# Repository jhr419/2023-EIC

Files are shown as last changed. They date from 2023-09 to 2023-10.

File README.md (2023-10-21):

# BUPT EIC  

北京邮电大学鸿雁战队2023工程创新与实践大赛电控代码仓库

## 使用说明

上电后，调整机械臂到指定位置后，按下A版上的白键锁定

### 通信接口说明

---

usart6 - 与NUC的收发和交流\
uart8 - 与action的收发和交流\
uart7 - 调试使用接口\
can - 和电机交互\
can1 - MS4015\
can2 - M2006&M3508

---

## Work To be done & optimized

· **待完成** 影响是否能够完成项目的事项\
1.完成2006ECD锁定\
2.添加转盘函数\
这俩做完就差不多做完了\
· **待优化** 对已有的功能进行性能提高/模块解耦/可维护性增强\
1.任务延时调整\
2.任务流程优化\
2.2006 pid调整\
· **待添加** 无关紧要，锦上添花

## 开发准则

### 禁止过度摸鱼

### 禁止在临界区使用os延迟

#### 临界资源

指一次仅仅允许一个线程访问的共享资源，它可以是一个具体的硬件设备，也可以是一个变量，可以是缓冲区等，这些都称为临界资源，或者共享资源，多个任务同时运行，只能允许一个任务访问的资源。

#### 临界区

每个进程中访问临界资源的那段代码称为临界区，
每次只允许一个进程进入临界区，进入后，不允许其他进程进入。不论是硬件临界资源还是软件临界资源，多个进程必须互斥的对它进行访问。多个进程涉及到同一个临界资源的的临界区称为相关临界区。使用临界区时，一般不允许其运行时间过长，只要运行在临界区的线程还没有离开，其他所有进入此临界区的线程都会被挂起而进入等待状态。

### 禁止在使用开发版自带的xt30接口接电机

电机的反向电动势可能会烧毁开发板。

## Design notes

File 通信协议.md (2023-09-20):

# 通信协议 v1.0

## 串口配置

通信方式是串口，配置为波特率 115200，8 位数据位，1 位停止位，无硬件流控，无校验位。

## 通信协议格式

|帧头|数据|帧尾|
|:-:|:-:|:-:|
|frame_header(5-Byte)|data(n-Byte)|frame_tail(2-Byte,CRC-16,仅校验data)|

## frame_header格式

|SOF|cmd_id|length|CRC-8|
|:-:|:-:|:-:|:-:|
|0xA5(1-Byte)|命令码(1-Byte)|data长度(2-Byte)|帧头校验(1-Byte)|

## 命令码说明

|cmd_id|数据类型|
|:-:|:-:|
|0x01|trolley_info_t|
|0x02|move_cmd_t|
|0x03|pinch_cmd_t|

## 数据类型详情

    typedef struct
    {
        float32 x_abs;
        float32 y_abs;
        float32 angle_abs; // 角度制
        int16_t block_num; // 车载物块数量，上限为3
    } trolley_info_t;

上述坐标以下图坐标系为参考，角度信息以x轴正方向为0度，取值范围（-180,180]。
（下图仅作示意，具体位置待实际测量）
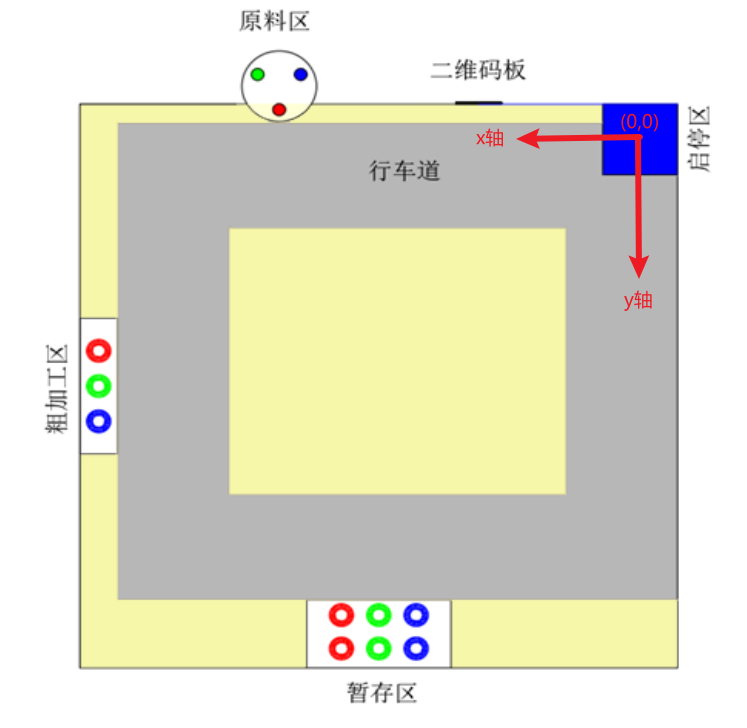
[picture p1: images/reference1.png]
reference1


    typedef struct
    {
        float32 vx_err;
        float32 vy_err;
        float32 vw_err;
    } move_cmd_t;

上述信息均为相对值，相对于车的当前位置及朝向。或者说，是可以直接用于PID算法的error值。

    typedef struct
    {
        uint8_t act_id; // act_id对应动作编号（1-抓取，2-放置）
    } pinch_cmd_t;

 ## 动作编号说明

|cmd_id|数据类型|
|:-:|:-:|
|0x01|ARM1_GRAP1|
|0x02|ARM2_GRAP1|
|0x03|ARM2_PLACE1|
|0x04|ARM2_PLACE2|

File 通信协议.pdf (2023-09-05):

通信协议.md | 9/4/2023

# 通信协议

## 串⼝配置

通信⽅式是串⼝，配置为波特率 115200，8 位数据位，1 位停⽌位，⽆硬件流控，⽆校验位。

## 通信协议格式

帧头 | 数据 | 帧尾
frame_header(5-Byte) data(n-Byte) frame_tail(2-Byte,CRC-16,仅校验data)

## frame_header格式

SOF | cmd_id | length | CRC-8

0xA5(1-Byte) 命令码(1-Byte) data⻓度(2-Byte) 帧头校验(1-Byte)

## 命令码说明

cmd_id | 数据类型
0x01 | trolley_info_t
0x02 | move_cmd_t
0x03 | pinch_cmd_t

## 数据类型详情

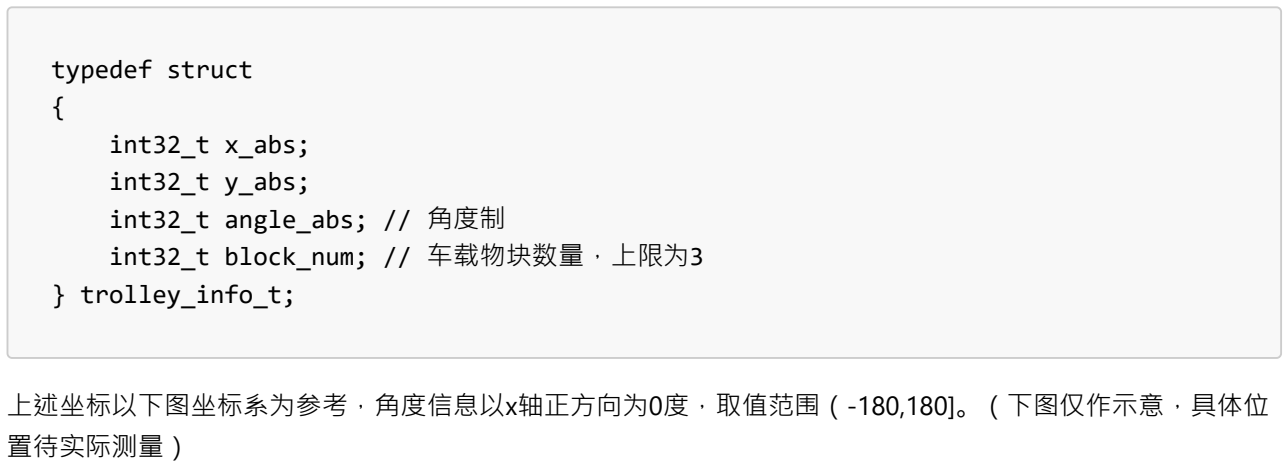
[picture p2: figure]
typedef struct {; int32_t x_abs; int32_t y_abs; int32_t angle_abs; // ⾓度制 int32_t block_num; // ⻋载物块数量，上限为3 } trolley_info_t;; 上述坐标以下图坐标系为参考，⾓度信息以x轴正⽅向为0度，取值范围（-180,180]。 （下图仅作⽰意，具体位 置待实际测量）

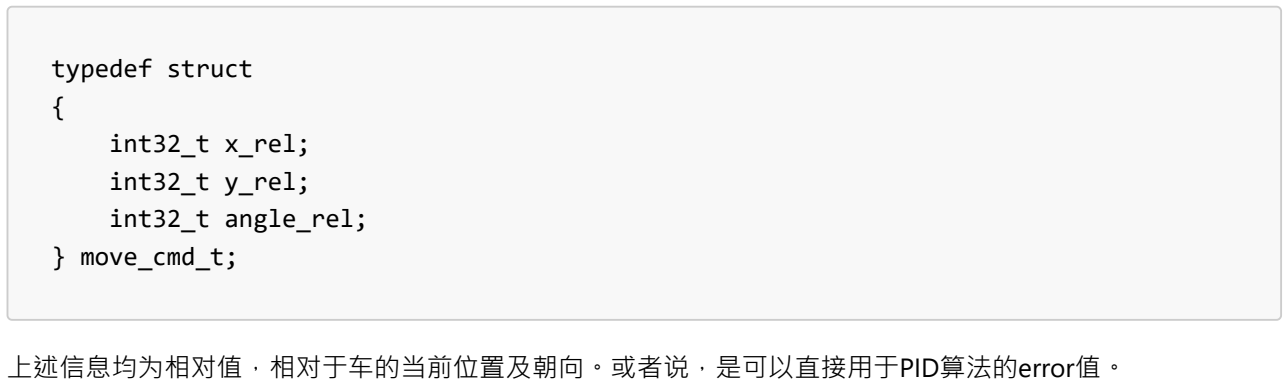
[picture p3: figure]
typedef struct {; int32_t x_rel; int32_t y_rel; int32_t angle_rel; } move_cmd_t;; 上述信息均为相对值，相对于⻋的当前位置及朝向。或者说，是可以直接⽤于PID算法的error值。
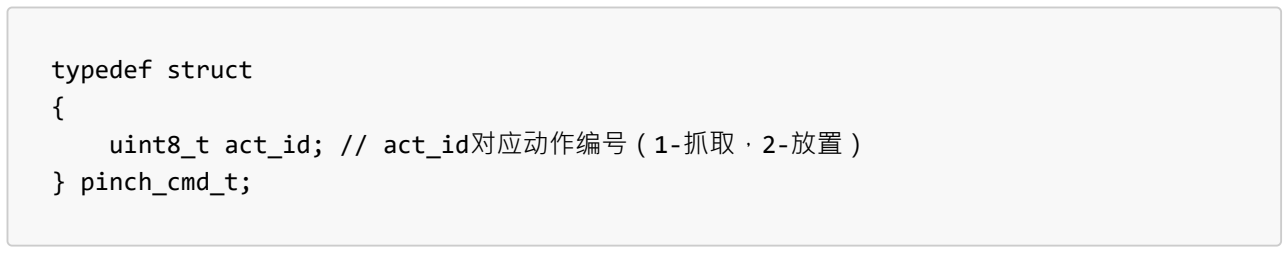
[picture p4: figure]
typedef struct {; uint8_t act_id; // act_id对应动作编号（1-抓取，2-放置） } pinch_cmd_t;

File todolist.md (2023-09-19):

任务流程汇总
全场定位坐标转换为整车坐标 这部分代码得今天完成
1. pid算法选择
2. 速度规划算法（简单方案，复杂方案）现敲定以双环pid，或者位置环+读取编码器的值获取
3. 底盘任务（跑定点 ，旋转固定角度同时走位置 , 换算坐标）
4. 舵机的控制及设计抓取和放置流程（打开不同电机计时器，设置pid控制）
5. 机械臂任务目前有四种，抓取台上物品，抓取车上物块，放置在地上，放置在物块上

这次需要突破的问题，就是将以前的模糊值转化为真实值
然后制定完整的机器人框架，将代码写成库的形式，可能需要审视一下代码，将其中复用性差的部分移除

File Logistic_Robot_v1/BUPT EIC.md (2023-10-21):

# BUPT EIC  

北京邮电大学鸿雁战队2023工程创新与实践大赛电控代码仓库

## 使用说明

上电后，调整机械臂到指定位置后，按下A版上的白键锁定

## 机械臂动作说明

### 旋转2006简称Ⅰ，升降2006简称Ⅱ

#### 运行前需Ⅰ要标定的位置

| 编号 | a | b |
| :-----:| :----: |  :----: |
| 描述 | 向内 |向外|

起始位置应该与机械臂最近的一条边垂直，且正对着4015载物盘

#### 运行前升降要标定的位置

| 编号 | 1 | 2 | 3 | 4 | 5 | 6 | 7 | 8 |
| :-----:| :----: | :----: | :----: | :----: | :----: | :----: | ---| ---|
| 描述 | 车内物料抓取预备点 |车内物料抓取点| 原料区物料抓取预备点 |原料区物料抓取点 | 地面物料预备点 | 地面取放点 | 细加工区叠放预备点 | 细加工区放置点 |

---

### 机械臂任务码设计及流程

基本动作：

1. arm底盘旋转：初始化，向外，向内

2. 升降机构：初始化（车上物料盘），向上，向下

3. 物料盘：初始化，物料加一

4. 摄像头舵机：二维码位置，物料位置

5. 机械爪：打开，关闭

### 启动区

task0: 初始化任务：

	物料底盘初始化，arm底盘初始化，升降初始化（略高于物料），舵机二维码位置

### 二维码区

task1：读取二维码任务：

	arm底盘向外， 机械爪打开

### 原料区

{

	task2：预抓取：

		 舵机物料位置，升降预备抓取位置，（车预备位置）

	task3：原料区抓取：

		升降降低位置，机械爪关闭

	task4：物料放置车上：

		升降抬升位置，arm底盘向内，升降降低至放置位置，机械爪打开，升降抬升

	task5：

		物料加一

}

task2-5执行三次

### 粗加工区

{

	task6：预放置：

		arm底盘向内，升降初始化（略高于物料），机械爪打开，物料盘转至对应物料，升降向下至物料处，机械爪关闭，升降抬升位置，arm底盘向外

	task7：放置：

		升降降低，机械爪打开，升降抬升

}

task6-7执行三次

{

	task8：预抓取：

		 arm底盘向外，升降预备抓取位置，（车预备位置）

	task9：抓取：

		升降降低位置，机械爪关闭

	task10：物料放置车上：

		升降抬升位置，arm底盘向内，升降降低至放置位置，机械爪打开

	task11：

		物料加一

}

task8-11执行三次

### 细加工区

{

	task12：预放置：

		arm底盘向内，升降初始化（略高于物料），机械爪打开，物料盘转至对应物料，升降向下至物料处，机械爪关闭，升降抬升位置，arm底盘向外

	task13：放置：

		升降降低，机械爪打开，升降抬升

}

task12-13执行三次

## 进入下一轮原料区

原料区、粗加工区任务重做

### 叠放

{

	task14：预放置：

		arm底盘向内，升降初始化（略高于物料），机械爪打开，物料盘转至对应物料，升降向下至物料处，机械爪关闭，升降抬升位置，arm底盘向外

	task15：放置：

		升降降低，机械爪打开，升降抬升

}

task14-15执行三次

### 通信接口说明

---

usart6 - 与NUC的收发和交流\
uart8 - 与action的收发和交流\
uart7 - 调试使用接口\
dbus - 遥控器接口\
can - 和电机交互\
can1 - MS4015\
can2 - M2006&M3508

---

## Work To be done & optimized

· **待完成** 影响是否能够完成项目的事项\
· **待优化** 对已有的功能进行性能提高/模块解耦/可维护性增强\
· **待添加** 无关紧要，锦上添花

## 开发准则

### 禁止过度摸鱼

### 禁止在临界区使用os延迟

#### 临界资源

指一次仅仅允许一个线程访问的共享资源，它可以是一个具体的硬件设备，也可以是一个变量，可以是缓冲区等，这些都称为临界资源，或者共享资源，多个任务同时运行，只能允许一个任务访问的资源。

#### 临界区

每个进程中访问临界资源的那段代码称为临界区，
每次只允许一个进程进入临界区，进入后，不允许其他进程进入。不论是硬件临界资源还是软件临界资源，多个进程必须互斥的对它进行访问。多个进程涉及到同一个临界资源的的临界区称为相关临界区。使用临界区时，一般不允许其运行时间过长，只要运行在临界区的线程还没有离开，其他所有进入此临界区的线程都会被挂起而进入等待状态。

### 禁止在使用开发版自带的xt30接口接电机

电机的反向电动势可能会烧毁开发板。

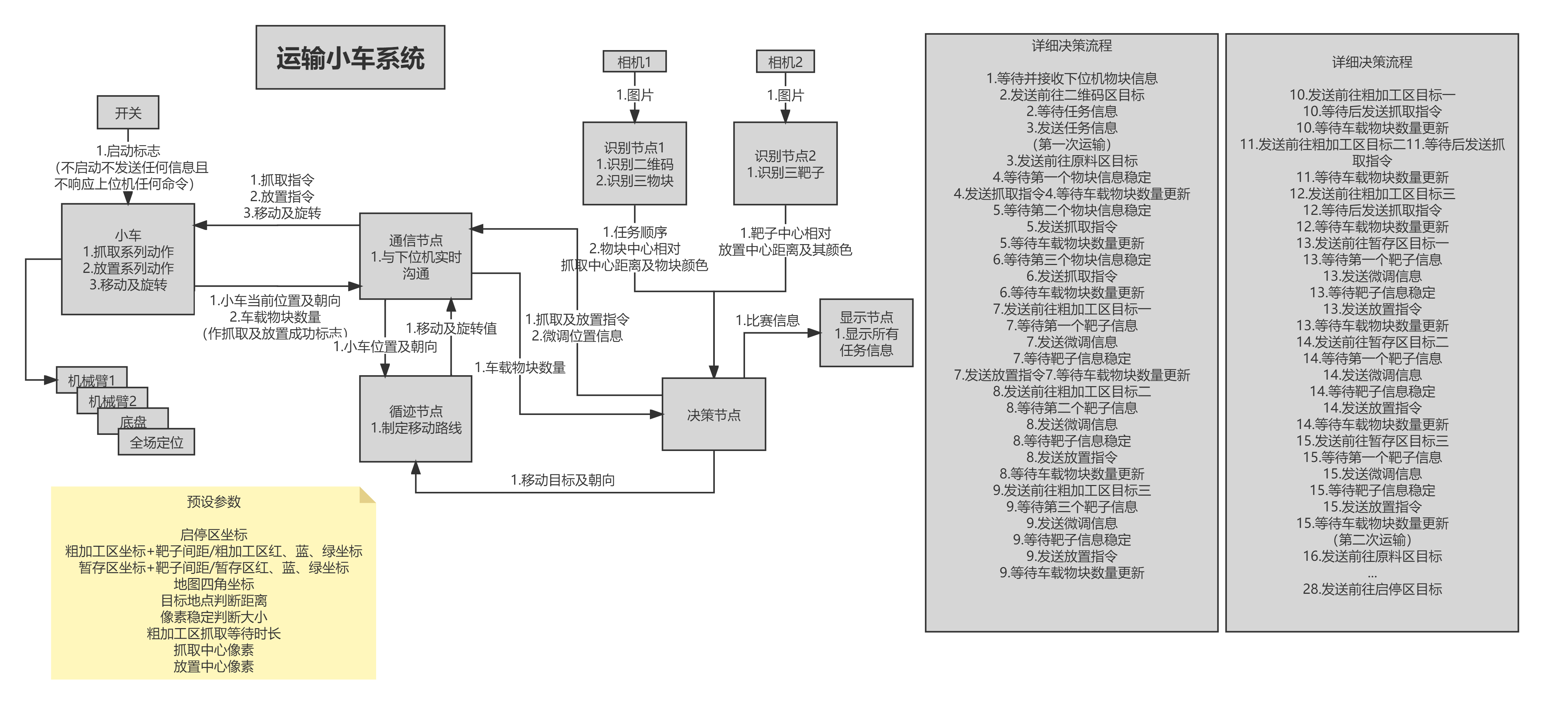
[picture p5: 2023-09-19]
程序框图.png

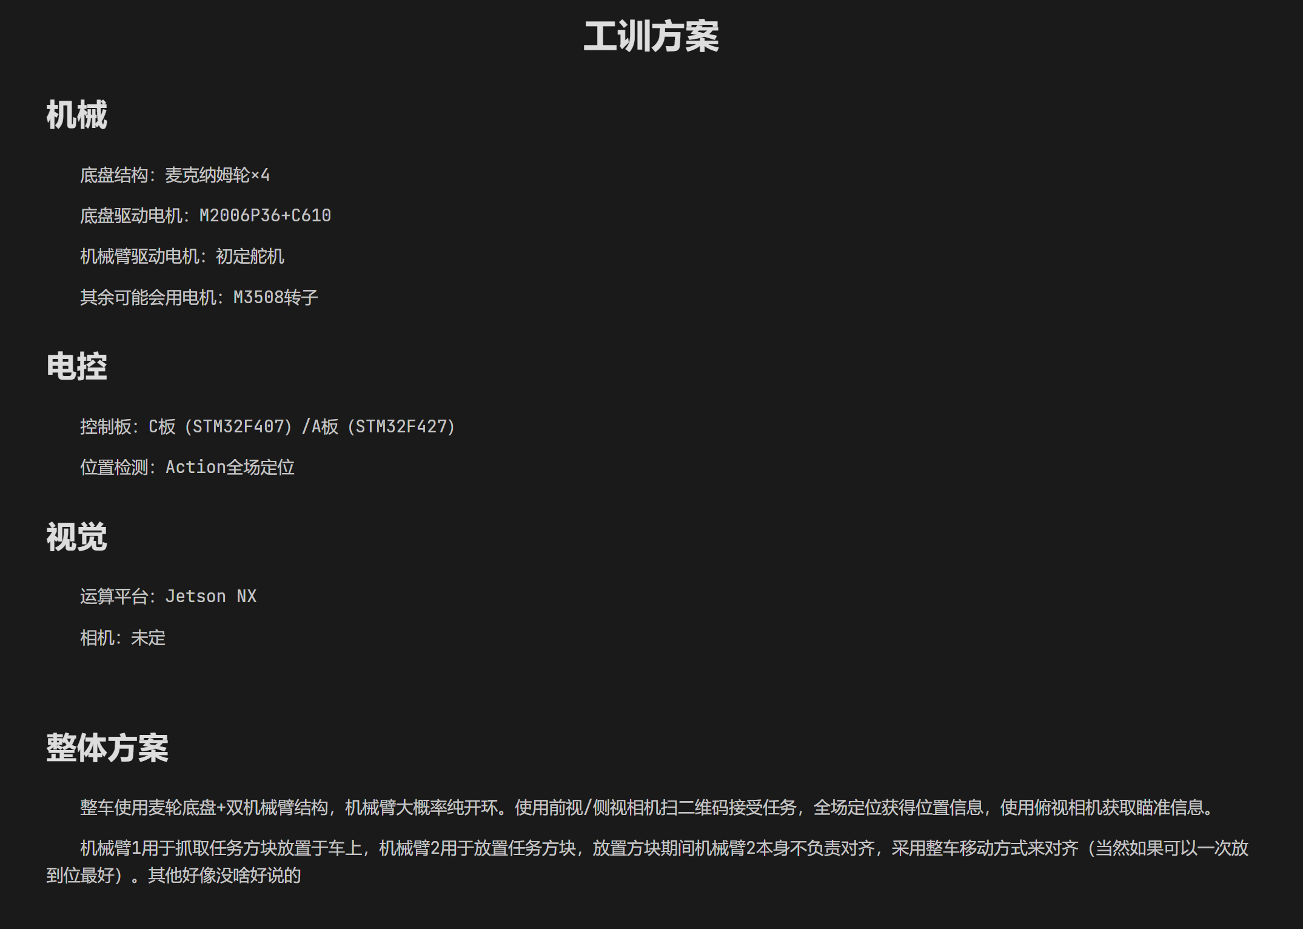
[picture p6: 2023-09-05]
规则性资料/工训.png

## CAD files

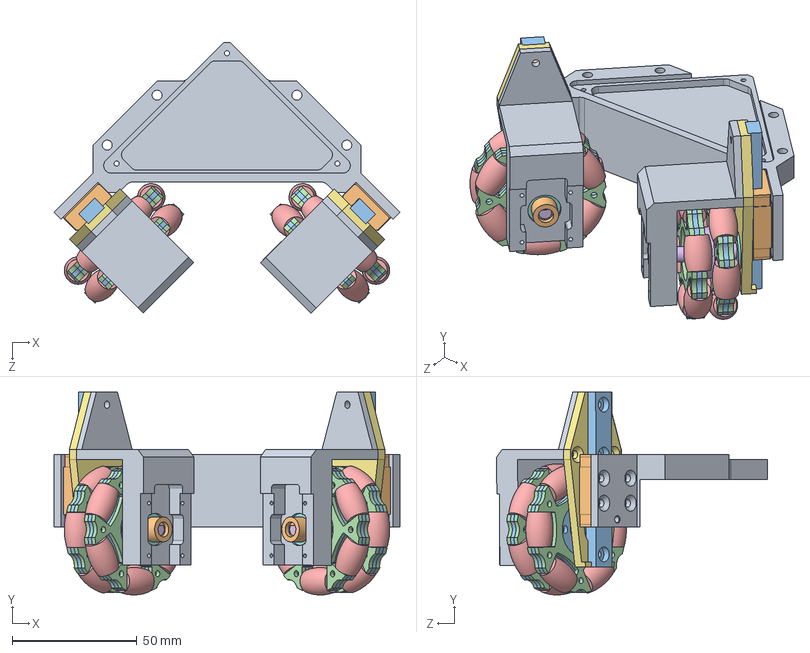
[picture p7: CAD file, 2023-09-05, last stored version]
自研全场定位资料v1.0/结构模型/两轮模型/全场定位自制/自制_总装.SLDASM
138.6 x 81.3 x 108.4 mm
自制_主体
自制_MGN9C滑块 x 2
自制_全向轮片2 x 4
自制_全向轮片1 x 8
自制_Action-从动滚轮 x 24
自制_全向轮连接轴 x 2
自制_滑轨固定件左 x 2
自制_Action-轴承1.0 x 4
自制_磁编码器固定 x 2
自制_6mm磁铁固定 x 2
自制_Action-导轨1.0 x 2

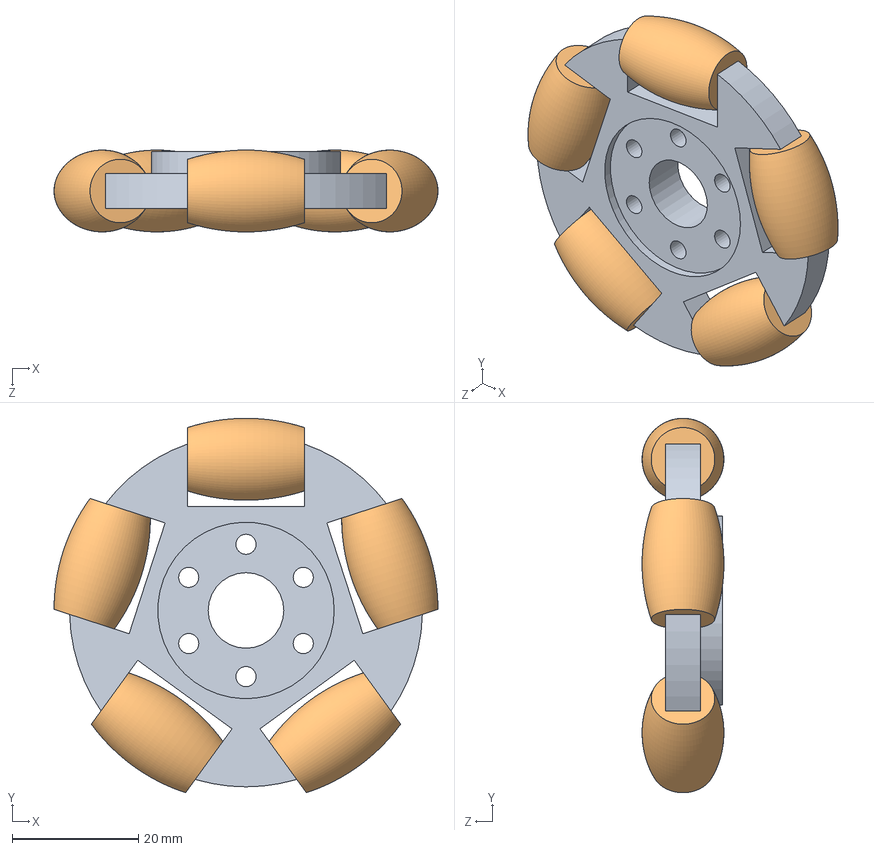
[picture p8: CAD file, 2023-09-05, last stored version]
自研全场定位资料v1.0/结构模型/两轮模型/三角码盘/三角码盘/Wheel_Half-60.SLDASM
61.0 x 59.4 x 13.0 mm
Wheel_Base-x
Wheel_x x 5

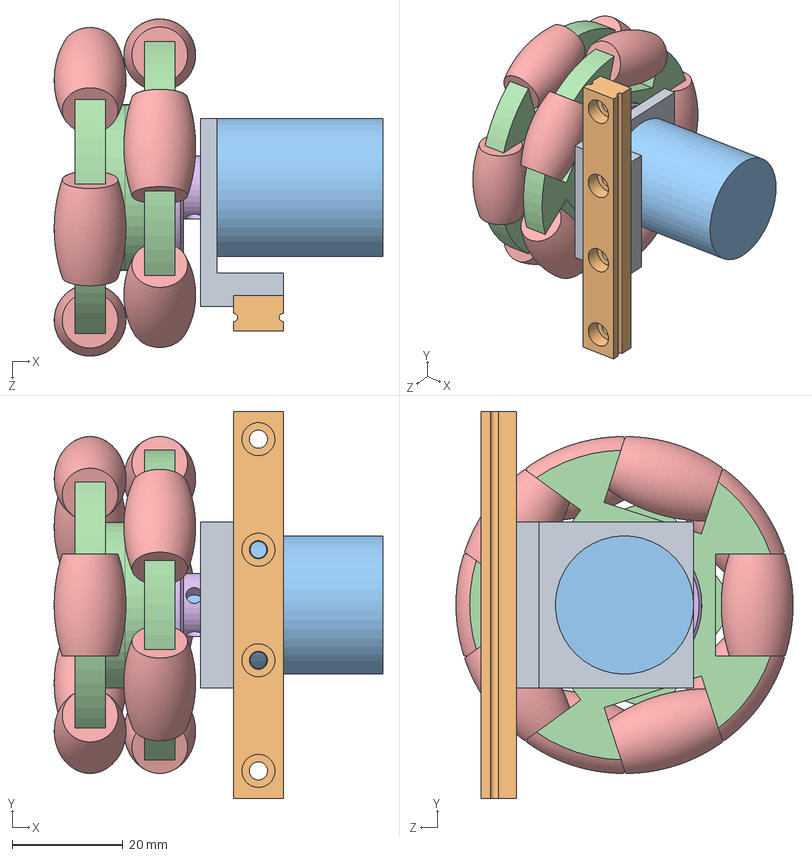
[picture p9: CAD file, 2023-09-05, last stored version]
自研全场定位资料v1.0/结构模型/两轮模型/三角码盘/三角码盘/码轮单侧.SLDASM
59.4 x 70.0 x 61.0 mm
码轮码盘支架
9mm导轨
小码盘
Wheel_Base-x x 2
Wheel_x x 10
Wheel法兰

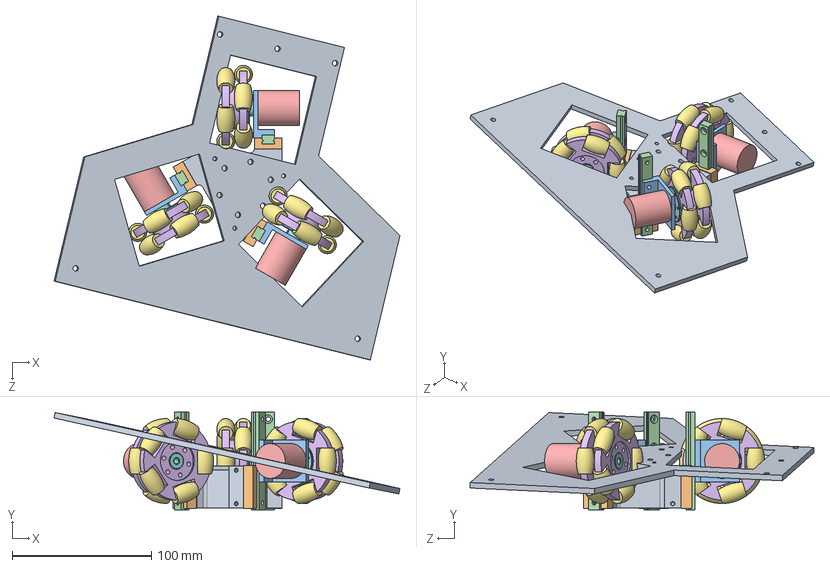
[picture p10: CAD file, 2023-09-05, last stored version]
自研全场定位资料v1.0/结构模型/两轮模型/三角码盘/三角码盘/三角码盘装配1.SLDASM
248.3 x 70.0 x 246.5 mm
三角码盘架
9mm滑块 x 3
码轮码盘支架 x 3
9mm导轨 x 3
小码盘 x 3
Wheel_Base-x x 6
Wheel_x x 30
Wheel法兰 x 3

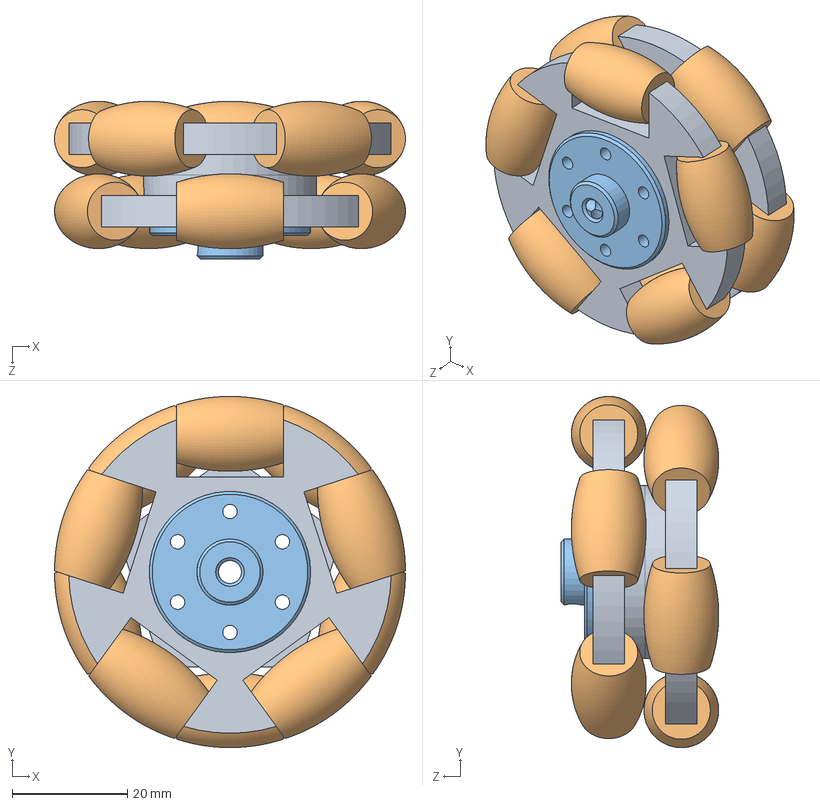
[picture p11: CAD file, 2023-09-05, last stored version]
自研全场定位资料v1.0/三轮定位资料/三轮模型/三角码盘/Wheel.SLDASM
61.0 x 61.0 x 27.3 mm
Wheel_Base-x x 2
Wheel_x x 10
Wheel法兰

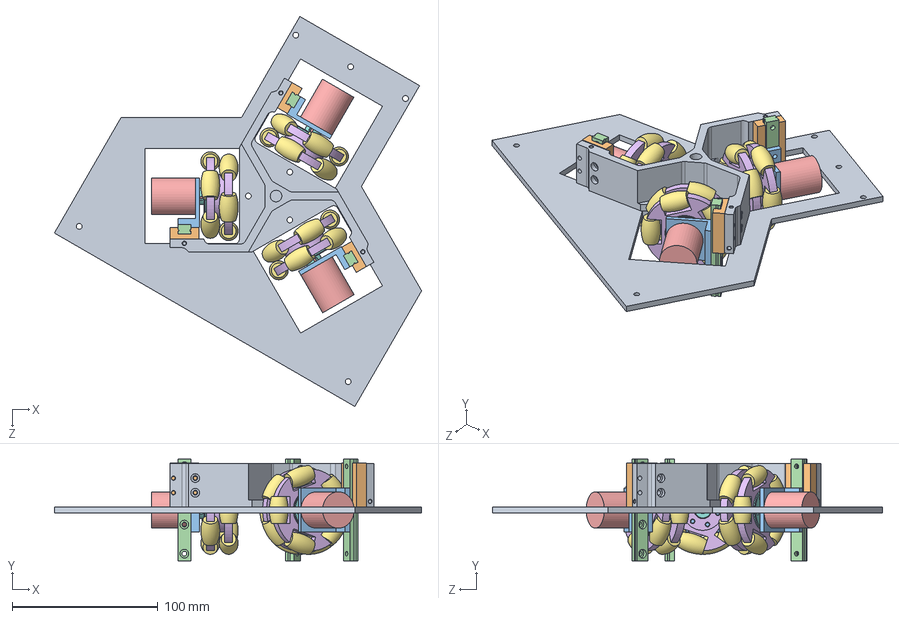
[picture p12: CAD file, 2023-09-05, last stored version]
自研全场定位资料v1.0/结构模型/两轮模型/三角码盘/三角码盘/三角码盘装配2.SLDASM
252.3 x 70.0 x 267.9 mm
三角码盘架2
9mm滑块 x 3
码轮码盘支架 x 3
9mm导轨 x 3
小码盘 x 3
Wheel_Base-x x 6
Wheel_x x 30
Wheel法兰 x 3
2号固定板

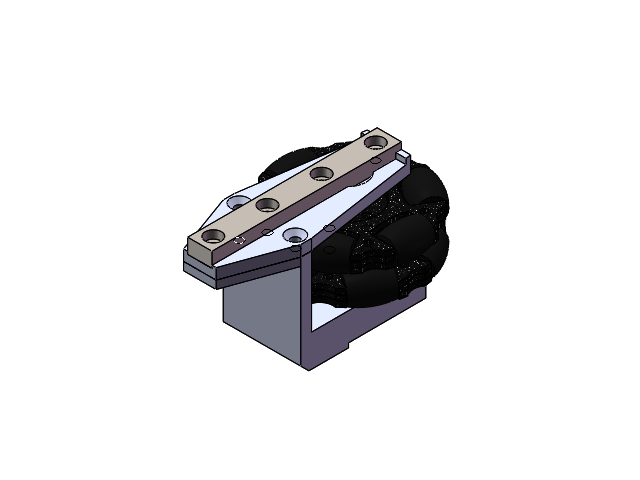
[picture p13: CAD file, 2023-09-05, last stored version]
自研全场定位资料v1.0/结构模型/两轮模型/全场定位自制/自制_轮系装配.SLDASM
自制_全向轮片2 x 2
自制_全向轮片1 x 4
自制_Action-从动滚轮 x 12
自制_全向轮连接轴
自制_滑轨固定件左
自制_Action-轴承1.0 x 2
自制_磁编码器固定
自制_6mm磁铁固定
自制_Action-导轨1.0

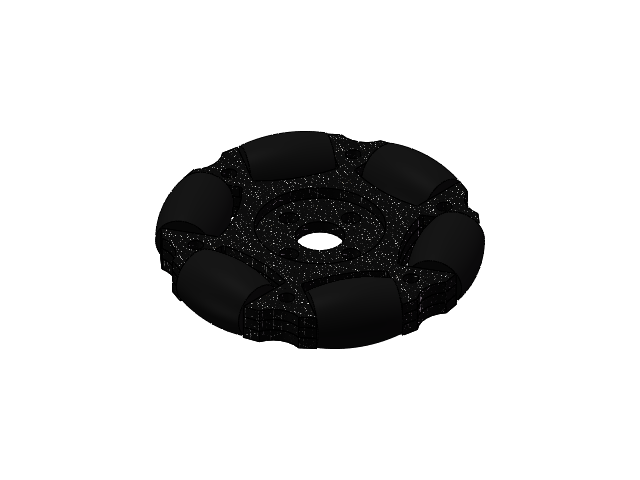
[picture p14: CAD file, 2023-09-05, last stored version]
自研全场定位资料v1.0/结构模型/两轮模型/全场定位自制/自制_全向轮轮片.SLDASM
自制_全向轮片2
自制_全向轮片1 x 2
自制_Action-从动滚轮 x 6

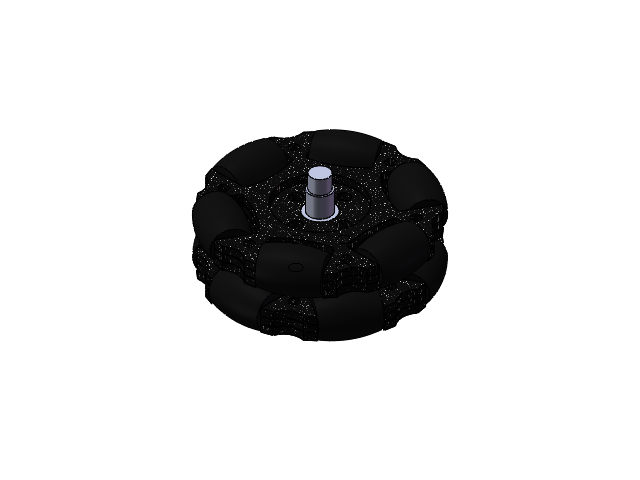
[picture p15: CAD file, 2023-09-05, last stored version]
自研全场定位资料v1.0/结构模型/两轮模型/全场定位自制/自制_全向轮装配.SLDASM
自制_全向轮片2 x 2
自制_全向轮片1 x 4
自制_Action-从动滚轮 x 12
自制_全向轮连接轴

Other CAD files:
自研全场定位资料v1.0/结构模型/两轮模型/总装/全向轮装配.SLDASM
自研全场定位资料v1.0/结构模型/两轮模型/总装/轮系装配.SLDASM
自研全场定位资料v1.0/结构模型/两轮模型/总装/全向轮轮片.SLDASM
自研全场定位资料v1.0/结构模型/两轮模型/总装/总装.SLDASM
自研全场定位资料v1.0/三轮定位资料/三轮模型/三角码盘/2号固定板.SLDPRT
自研全场定位资料v1.0/三轮定位资料/三轮模型/三角码盘/7直线导轨滑块.SLDPRT
自研全场定位资料v1.0/三轮定位资料/三轮模型/三角码盘/7短直线导轨.SLDPRT
自研全场定位资料v1.0/三轮定位资料/三轮模型/三角码盘/9mm导轨.SLDPRT
自研全场定位资料v1.0/三轮定位资料/三轮模型/三角码盘/9mm滑块.SLDPRT
自研全场定位资料v1.0/三轮定位资料/三轮模型/三角码盘/Wheel_Base-x.SLDPRT
自研全场定位资料v1.0/三轮定位资料/三轮模型/三角码盘/Wheel_x .SLDPRT
自研全场定位资料v1.0/三轮定位资料/三轮模型/三角码盘/Wheel法兰.SLDPRT
自研全场定位资料v1.0/三轮定位资料/三轮模型/三角码盘/v码盘.SLDPRT
自研全场定位资料v1.0/三轮定位资料/三轮模型/三角码盘/三角码盘架.SLDPRT
自研全场定位资料v1.0/三轮定位资料/三轮模型/三角码盘/三角码盘架2.DWG
自研全场定位资料v1.0/三轮定位资料/三轮模型/三角码盘/三角码盘架2.SLDDRW
自研全场定位资料v1.0/三轮定位资料/三轮模型/三角码盘/三角码盘架2.SLDPRT
自研全场定位资料v1.0/三轮定位资料/三轮模型/三角码盘/小码盘.SLDPRT
自研全场定位资料v1.0/三轮定位资料/三轮模型/三角码盘/码轮码盘支架.SLDPRT
自研全场定位资料v1.0/结构模型/两轮加工件/主体.STEP
自研全场定位资料v1.0/结构模型/两轮加工件/全向轮连接轴.STEP
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

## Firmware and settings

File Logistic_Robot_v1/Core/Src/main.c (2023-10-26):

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
/* Includes ------------------------------------------------------------------*/
#include "main.h"
#include "cmsis_os.h"
#include "can.h"
#include "dma.h"
#include "tim.h"
#include "usart.h"
#include "gpio.h"

/* USER CODE BEGIN Includes */
#include <stdarg.h>
#include <stdio.h>

#include <stdlib.h>
#include "commu_task.h"
#include "struct_typedef.h"
#include "bsp_usart.h"
#include "chassis_task.h"
#include "servo_task.h"
#include "CAN_receive.h"
#include "CAN_cmd_all.h"
#include "gear_motor_ctrl.h"
#include "bsp_can.h"
#include "servo.h"
#include "motor_ctrl.h"

extern uint8_t cnt;
extern UART_HandleTypeDef huart6;
void usart_printf(const char *fmt,...)
{
    static uint8_t tx_buf[256] = {0};
    static va_list ap;
    static uint16_t len;
    va_start(ap, fmt);
		
    len = vsprintf((char *)tx_buf, fmt, ap);

    va_end(ap);

		HAL_UART_Transmit(&huart6, tx_buf, len, 100);
    usart6_tx_dma_enable(tx_buf, len);

}
/* USER CODE END Includes */


/* USER CODE BEGIN PV */
extern servo_t servo[8];
extern const motor_6020_measure_t*	motor_6020;

/* USER CODE END PV */

void SystemClock_Config(void);
void MX_FREERTOS_Init(void);
/**
  * @brief  The application entry point.
  * @retval int
  */
int main(void)
{
  /* USER CODE BEGIN 1 */
	uint8_t rising_falling_flag1 ;
  /* USER CODE END 1 */

  /* MCU Configuration--------------------------------------------------------*/

  /* Reset of all peripherals, Initializes the Flash interface and the Systick. */
  HAL_Init();

  /* Configure the system clock */
  SystemClock_Config();

  /* Initialize all configured peripherals */
  MX_GPIO_Init();
  MX_DMA_Init();
  MX_UART8_Init();
  MX_USART6_UART_Init();
  MX_CAN1_Init();
  MX_TIM2_Init();
  MX_TIM8_Init();
  MX_UART7_Init();
  MX_CAN2_Init();
  /* USER CODE BEGIN 2 */
	can_filter_init();
	servo_init(); 
	CAN_angleControl(CAN_M1_ID, 0);
	angle_m6020_init();
  /* USER CODE END 2 */

  /* Call init function for freertos objects (in freertos.c) */
  MX_FREERTOS_Init();

  /* Start scheduler */
  osKernelStart();

  /* We should never get here as control is now taken by the scheduler */
  /* Infinite loop */
  /* USER CODE BEGIN WHILE */
	while(1){
    /* USER CODE END WHILE */

    /* USER CODE BEGIN 3 */

	}
  /* USER CODE END 3 */
}

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


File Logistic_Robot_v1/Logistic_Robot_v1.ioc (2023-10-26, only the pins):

Mcu.UserName=STM32F427IIHx
PA0/WKUP.Signal=S_TIM2_CH1_ETR
PA1.Signal=S_TIM2_CH2
PA13.Signal=SYS_JTMS-SWDIO
PA14.Signal=SYS_JTCK-SWCLK
PA2.Signal=S_TIM2_CH3
PA3.Signal=S_TIM2_CH4
PB12.Signal=CAN2_RX
PB13.Signal=CAN2_TX
PB2/BOOT1.GPIO_Label=KEY
PB2/BOOT1.Signal=GPXTI2
PD0.Signal=CAN1_RX
PD1.Signal=CAN1_TX
PE0.Signal=UART8_RX
PE1.Signal=UART8_TX
PE7.Signal=UART7_RX
PE8.Signal=UART7_TX
PG1.GPIO_Label=ACTION_LED
PG1.Signal=GPIO_Output
PG14.Signal=USART6_TX
PG9.Signal=USART6_RX
PH0/OSC_IN.Signal=RCC_OSC_IN
PH1/OSC_OUT.Signal=RCC_OSC_OUT
PH2.Signal=GPIO_Output
PH3.Signal=GPIO_Output
PH4.Signal=GPIO_Output
PH5.Signal=GPIO_Output
PI0.GPIO_Label=BUTTON
PI0.Signal=GPXTI0
PI5.Signal=S_TIM8_CH1

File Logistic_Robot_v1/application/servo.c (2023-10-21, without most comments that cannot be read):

#include "servo.h"
#include "string.h"
#include "tim.h"
#include "main.h"



extern TIM_HandleTypeDef htim2;
extern TIM_HandleTypeDef htim8;

servo_t servo[8];

void servo_init(void)
{
	HAL_TIM_Base_Start(&htim2);
	HAL_TIM_PWM_Start(&htim2,TIM_CHANNEL_1);
	HAL_TIM_PWM_Start(&htim2,TIM_CHANNEL_2);
	HAL_TIM_PWM_Start(&htim2,TIM_CHANNEL_3);
	HAL_TIM_PWM_Start(&htim2,TIM_CHANNEL_4);
	
	HAL_TIM_Base_Start(&htim8);
	HAL_TIM_PWM_Start(&htim8,TIM_CHANNEL_1);
	HAL_TIM_PWM_Start(&htim8,TIM_CHANNEL_2);
	HAL_TIM_PWM_Start(&htim8,TIM_CHANNEL_3);
	HAL_TIM_PWM_Start(&htim8,TIM_CHANNEL_4);
	
	for(int i=0;i<4;i++)
	{
		servo[i].htim = UESR_HTIM1;
		servo[i].id = i+1;
		servo[i+4].htim = UESR_HTIM2;
		servo[i+4].id = i+5;
	}
	
	servo[0].channel = TIM_CHANNEL_1;
	servo[1].channel = TIM_CHANNEL_2;
	servo[2].channel = TIM_CHANNEL_3;
	servo[3].channel = TIM_CHANNEL_4;
	servo[4].channel = TIM_CHANNEL_1;
	servo[5].channel = TIM_CHANNEL_2;
	servo[6].channel = TIM_CHANNEL_3;
	servo[7].channel = TIM_CHANNEL_4;
}

servo_t* get_servo_point(int i){
	return &servo[i];
}
void single_servo_ctrl(servo_t* servo, uint16_t pwm)
{
	TIM_HandleTypeDef htim = servo->htim;
	uint32_t channel = servo->channel;
	//uint32_t pwm = COMPARE_PER_ANGLE * angle;
	__HAL_TIM_SetCompare(&htim, channel, pwm);
}

void arm_ready(void)
{
		single_servo_ctrl(&servo[0], 600);
		single_servo_ctrl(&servo[1],300);
		single_servo_ctrl(&servo[2],930);
  	single_servo_ctrl(&servo[3],1000);
}

void arm_catch(void)
{
		single_servo_ctrl(&servo[0], 580);//ץȡ
		single_servo_ctrl(&servo[1],350);
		single_servo_ctrl(&servo[2],910);
		single_servo_ctrl(&servo[3],1160);
}

void arm_put_ready(void)
{
			single_servo_ctrl(&servo[0], 1050);
			single_servo_ctrl(&servo[1],330);
			single_servo_ctrl(&servo[2],450);
			single_servo_ctrl(&servo[3],1160);
}

void arm_up(void)
{
		single_servo_ctrl(&servo[0], 1058);
		single_servo_ctrl(&servo[1],350);
		single_servo_ctrl(&servo[2],430);
		single_servo_ctrl(&servo[3],1160);
}

void arm_put(void)
{
		single_servo_ctrl(&servo[0], 1058);
		single_servo_ctrl(&servo[1],350);
		single_servo_ctrl(&servo[2],430);
		single_servo_ctrl(&servo[3],1000);
}

void arm_put_stuff(void)
{
	single_servo_ctrl(&servo[0], 580);
	single_servo_ctrl(&servo[1],600);
	single_servo_ctrl(&servo[2],600);
	single_servo_ctrl(&servo[3],1160);
	
	HAL_Delay(2000);
	
	single_servo_ctrl(&servo[0], 500);//ץȡ
	single_servo_ctrl(&servo[2],1200);
	HAL_Delay(500);
	single_servo_ctrl(&servo[1],330);

	single_servo_ctrl(&servo[3],1160); 
	
	HAL_Delay(2000);
	
	
	
	single_servo_ctrl(&servo[0], 300);//ץȡ
	single_servo_ctrl(&servo[1],400);
	single_servo_ctrl(&servo[2],1100);
	single_servo_ctrl(&servo[3],1160); 
	
	HAL_Delay(1000);
	single_servo_ctrl(&servo[0], 300);//ץȡ
	single_servo_ctrl(&servo[1],400);
	single_servo_ctrl(&servo[2],1100);
	
	single_servo_ctrl(&servo[3],1000);
	
	
}	

void servo_angle_ctrl(servo_t* servo, uint16_t angle)
{
	TIM_HandleTypeDef htim = servo->htim;
	uint32_t channel = servo->channel;
	uint32_t pwm = COMPARE_PER_ANGLE * angle;
	__HAL_TIM_SetCompare(&htim, channel, 500+pwm);
}

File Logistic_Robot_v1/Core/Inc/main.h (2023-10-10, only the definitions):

#define BUTTON_Pin GPIO_PIN_0
#define BUTTON_GPIO_Port GPIOI
#define BUTTON_EXTI_IRQn EXTI0_IRQn
#define KEY_Pin GPIO_PIN_2
#define KEY_GPIO_Port GPIOB
#define KEY_EXTI_IRQn EXTI2_IRQn
#define ACTION_LED_Pin GPIO_PIN_1
#define ACTION_LED_GPIO_Port GPIOG

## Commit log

2023-09-05 配置第一个cube
2023-09-05 补充资料
    [2号固定板.SLDPRT, 6mm磁铁固定.SLDPRT, 7直线导轨滑块.SLDPRT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]
2023-09-07 加入板件支持包
2023-09-08 完成接收信息
2023-09-17 freertos 开好，通信任务完成
2023-09-18 can通信协议完成，如需更多命令码，详情请见电机can通信协议手册，自行添加
2023-09-18 调整文件夹
2023-09-19 加入arm数学库
2023-09-20 底盘任务完成、修改can命令码函数
2023-09-20 修改通信协议中变量命名
    底盘速度命名
2023-09-20 更改文件结构
2023-09-23 例行保存
2023-09-23 结点保存
2023-09-23 开始调pid
2023-09-23 调好pid
2023-09-24 开始写按钮
2023-09-24 回溯版本
2023-09-26 增加角度换算与按钮清零
2023-09-28 Y坐标标定完成，需要矫正X坐标
2023-10-01 servo_task结构初步完成
2023-10-10 servo功能函数完成，角度控制待验证
2023-10-10 保存 servo
2023-10-10 差2006任务函数，以及舵机的任务实现
2023-10-12 校赛结束
    差2006，等待机械臂结构
2023-10-15 增加圈数控制函数，并新添加一个任务
2023-10-15 修改一下README
2023-10-16 重构代码结构
2023-10-20 添加多M2006电机兼容
2023-10-20 增加按键启动2006
2023-10-20 readme更新
2023-10-21 更新README
    完成任务流程
2023-10-21 任务基本完成，能跑了
2023-10-21 重新规划任务
2023-10-21 小修小补
2023-10-22 基本任务流程完成，做优化
2023-10-24 写好6020
2023-10-26 交换跑点控制权
2023-10-26 保存一波
2023-10-27 北邮牛逼
2023-10-31 决赛最终

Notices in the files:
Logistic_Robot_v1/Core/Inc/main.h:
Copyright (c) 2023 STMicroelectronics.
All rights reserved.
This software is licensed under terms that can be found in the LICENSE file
